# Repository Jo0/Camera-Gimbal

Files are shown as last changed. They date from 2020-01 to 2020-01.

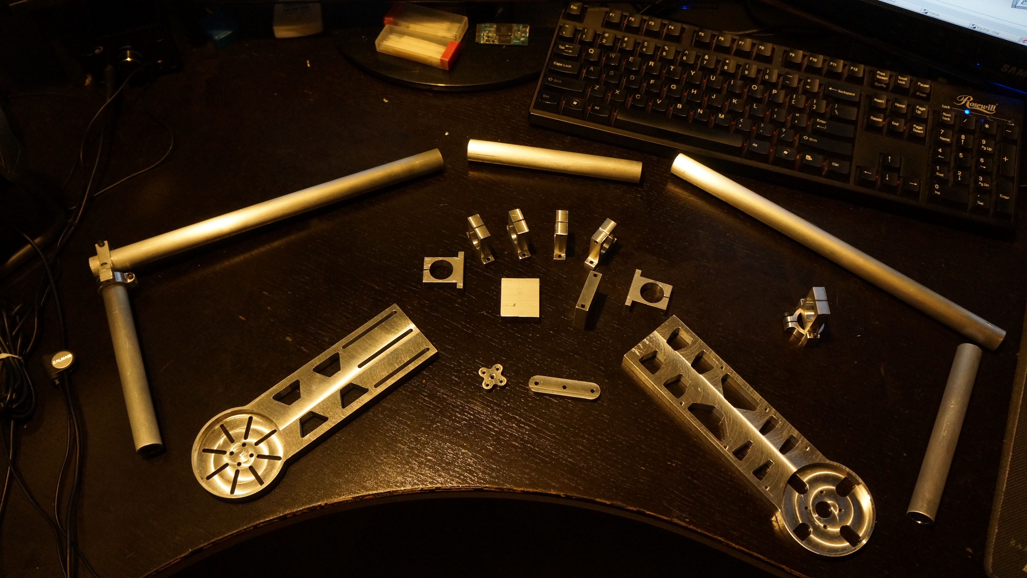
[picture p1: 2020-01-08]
Images/Machined Parts and Assembly/2 - QlwrPvh.jpg

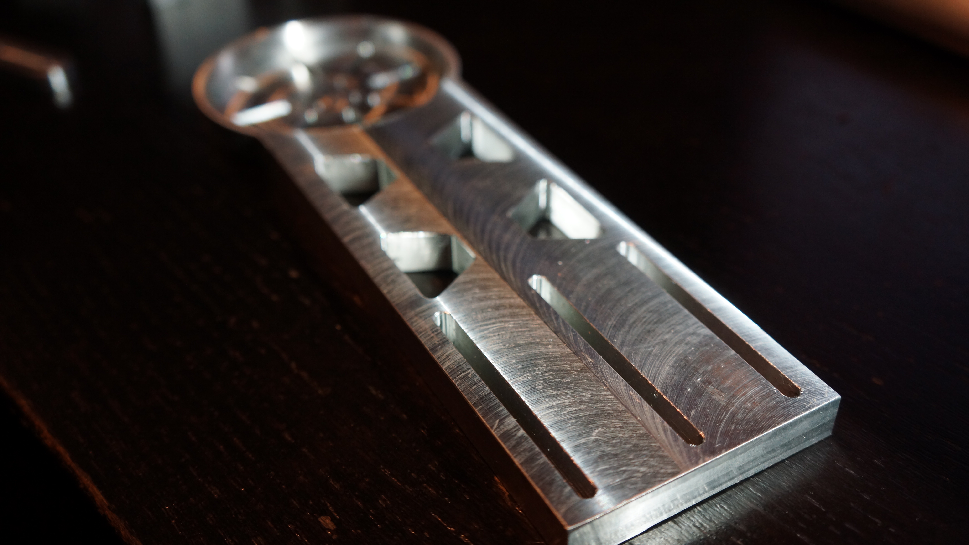
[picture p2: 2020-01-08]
Images/Machined Parts and Assembly/10 - DJeM7ET.jpg

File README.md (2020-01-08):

# Camera Gimbal

## Background

In 2014 I wanted to a camera gimbal. At the time, many great offerings were too expensive (~$500-700) and cheaper products had questionable quality and performance.

I took it upon myself to see if I could design and create my own. My girlfriend's dad (now father in law) is a machinist and was allowed to work on personal projects when off hours. Having no experience with using CAD software I was given access to a machine with SolidWorks and spent a week or so designing the various parts you see here in this repository.

## Materials

- 6061T6 Aluminium Sheet .190" thick
- 6061T6 Aluminium Sheet .750" diameter .125" thick wall
- M3 machine screws
- 685 2RS Premium ABEC3 Bearing 5 x 11 x 5 mm
- 3 x Turnigy HD 5208 Brushless Gimbal Motor
- Turnigy 2200mAh 3S 25C Lipo Pack
- EvvGC 1.3 Gimbal Controller Board with IMU (Inertial Measurement Unit)
  
## Electronics and Software

- EvvGC 1.3 Gimbal Controller Board with IMU (Inertial Measurement Unit)
- [EvvGC Firmware](https://github.com/Jo0/Firmware)
- [EvvGC Electronics](https://github.com/Jo0/Hardware)

## Outcome And Lessons Learned

- Images: 
  - [In this repository](https://github.com/Jo0/Camera-Gimbal/tree/master/Images)
  - [Machined parts and Assembly](https://imgur.com/a/h3jFl?)
  - [Renders](https://imgur.com/a/bzajgdB)
- Videos:
  - [YouTube Playlist Of Test Runs](https://www.youtube.com/playlist?list=PLFWRZ1I7BiI8qetZ2vBfIBI2kLMp9aT8P)
  
### 1. Picking up CAD is faily easy. Creating a good design is difficult

I didn't have a feedback loop of creating a design and prototyping it before finalizing the design. I pretty much relied on intuition (common sense), referencing other designs found online, the simulation of the assembled parts in SolidWorks, and eventually a final review with my father in law before finally machining the parts.

Although my design worked. I feel like I could've gotten a better result if I were able to actually have prototypes of each design iteration before "completing the project".

### 2. CNC Machining is not a magical and easy process

CNC Machining is not a process where you drop a material into a machine, press a button, and your part magically appears.

There's still quite a bit of human intervention in the process.
  - Understanding of materials and their use cases. 
  - Feasibility of the creation of the part(s) based on the design and the machining process(steps) that is necessary to achieve the end result.
  - Programming of the processes(steps) needed to create the part(s)
  - Precision of material and machine setup process

### 3. It's hard to keep costs down and produce a good result

One of the primary goals of the project was to keep costs down. I think I ended up spending ~$225 total to create the gimbal. The cost would've been significantly higher if I had to pay for a machinist to machine my part. Due to machine time and time spent programming the operations to create the parts.

I was able to cut costs on materials by
  - Not having multiple prototypes and only machining when the design was "finalized"
  - Not picking a more established gimbal controller
    - I chose the EvvGC gimbal controller due to the cost of the electronics (~$45) and that it was opensource
    - The other gimbal controller available at the time was the [AlexMos SimpleBGC Controller](https://shop.basecamelectronics.com/) ($150) and the various clone boards available at the time ($50)
      - I didn't want to take a chance on the clone boards due to reports on questionable compatibility on the software to interface with the controller at the time

### 4. There's more to a gimbal than just a frame, brushless motors, and a controller

Although I wanted the gimbal to magically stabilize my camera upon initial setup, I quickly found that there is more configuration to be done to get everything working perfectly.

1. Your gimbal must be balanced, to a reasonable degree, even when it's powered off for it to perform at a reasonable level.
   - While the controller can compensate for everything, it's better to think about the gimbal setup and the controller as an aid to the operator rather than a tool to compensate for the imbalance and instability of the entire system
2. Motor choice must match the load that you plan on putting on the gimbal system.
   - Luckily, I chose motors that were rated higher for the load I was putting on each axis of my gimbal. Had I had decided to choose lower rated motors to cut costs, I think I would've run into issues when mounting heavier cameras like a DSLR.
3. Motor PID tuning is delicate process
   - I may have had difficulty in this area due to the fact that I cut costs and chose an open source gimbal controller. I had a lot of trial and error when tuning the PID settings for the controller to properly control the rates at which the motors compensated for the movement across axes.

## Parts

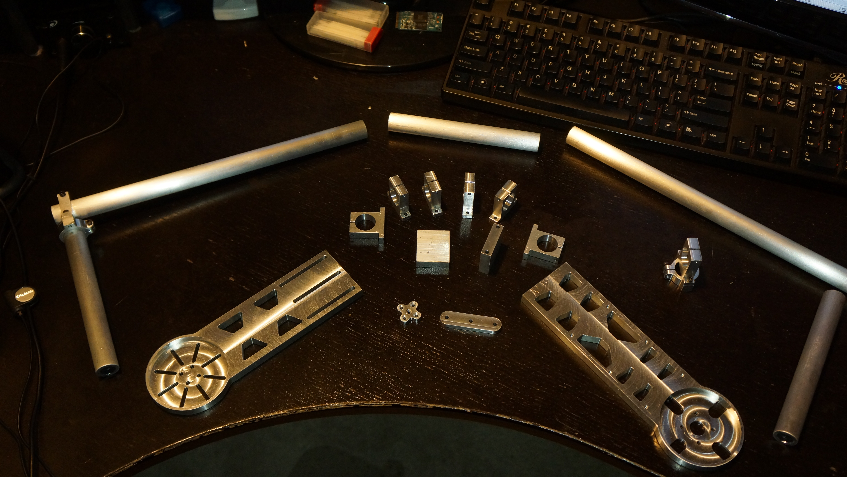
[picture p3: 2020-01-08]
Images/Machined Parts and Assembly/6 - cp2hWf3.jpg

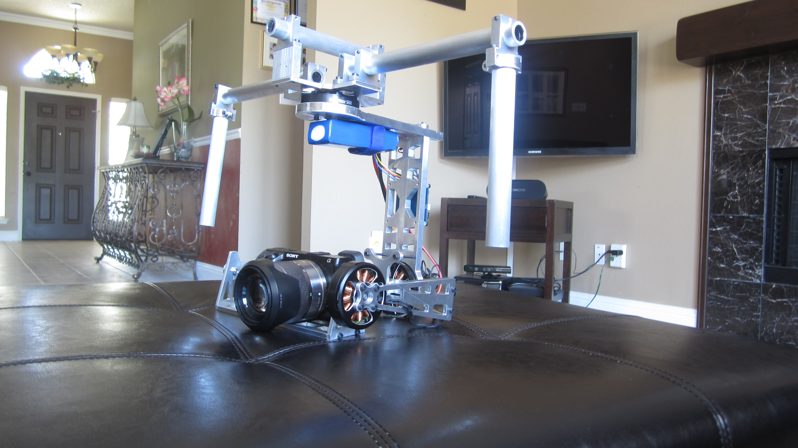
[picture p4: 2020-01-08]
Images/Machined Parts and Assembly/1 - EzWJhA9.jpg

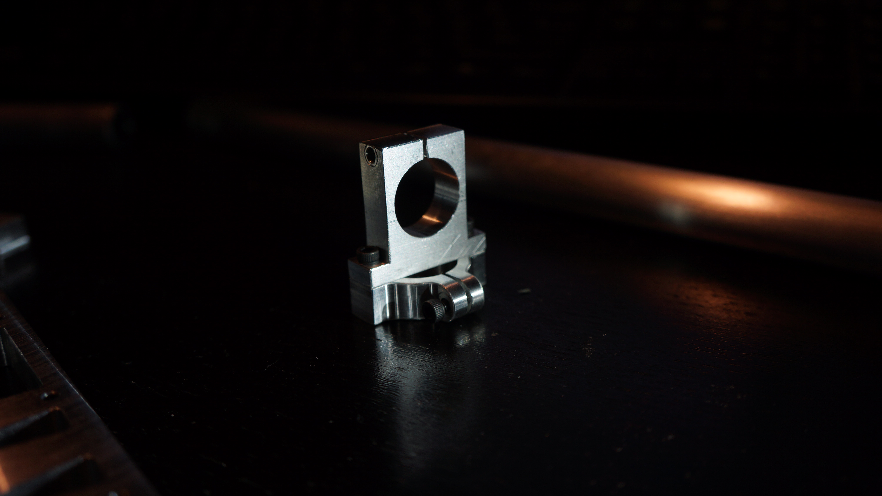
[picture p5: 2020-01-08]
Images/Machined Parts and Assembly/21 - t6TGg4F.jpg

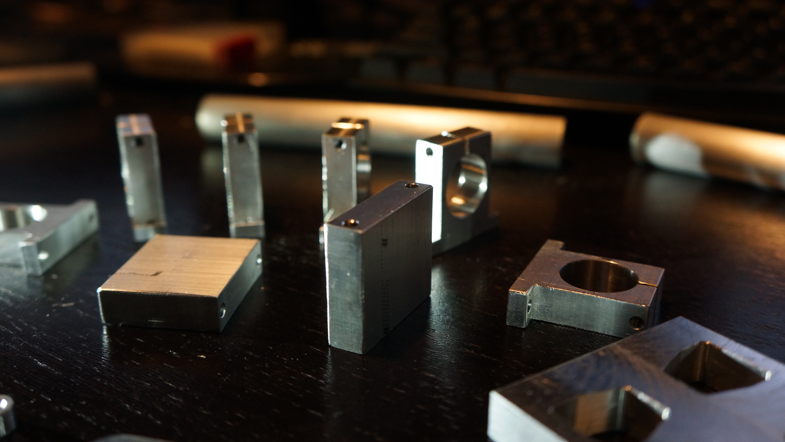
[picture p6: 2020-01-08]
Images/Machined Parts and Assembly/26 - 2xRYPu8.jpg

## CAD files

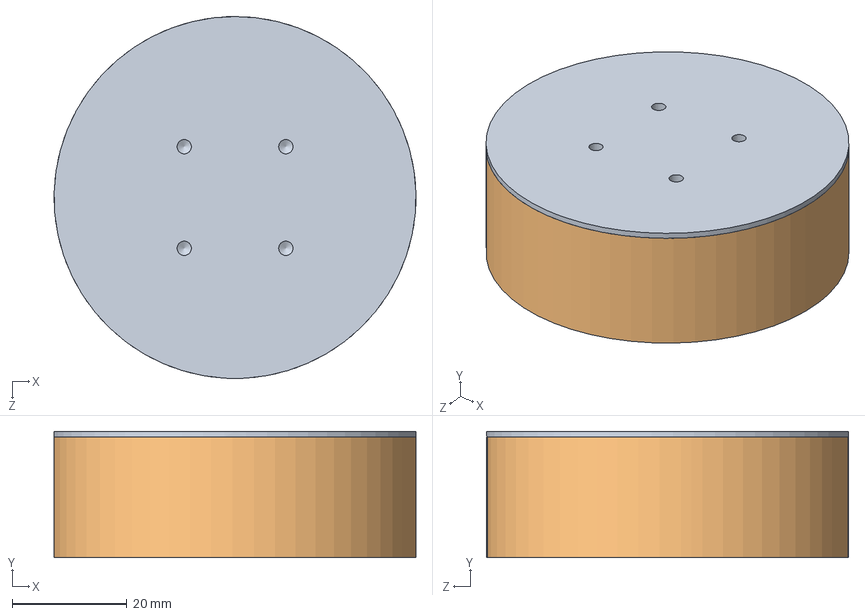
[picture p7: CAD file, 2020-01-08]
Motor Assm.SLDASM
63.0 x 22.0 x 63.0 mm
Mock Motor Bottom
Mock Motor Top

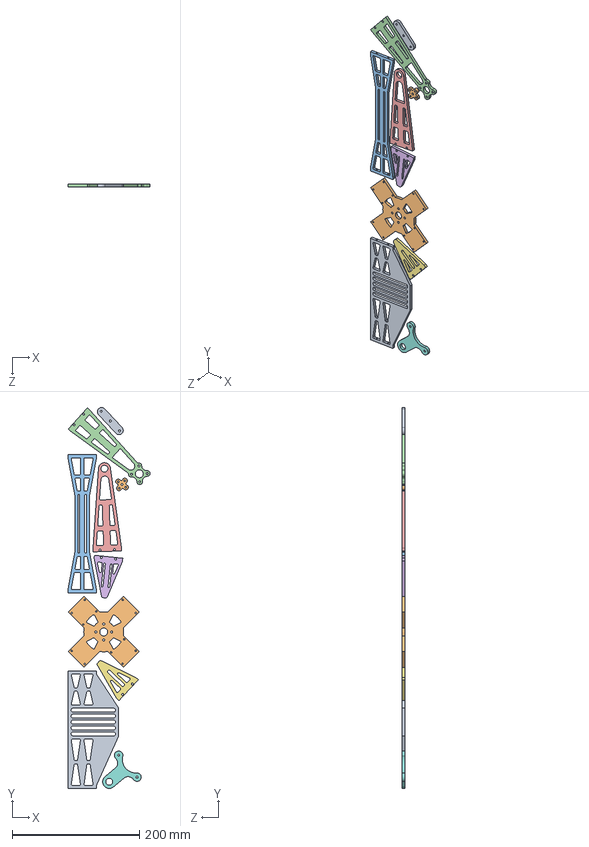
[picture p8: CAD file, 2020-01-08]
NestAssm-Gimbal-5mm.SLDASM
129.4 x 599.6 x 4.76 mm
Camera Tray
Handle Mount
Roll Bar
Pitch Arm Motor
Pitch Arm Bearing
Camera Tray Arm Motor
Camera Tray Arm Bearing
Roll Arm Bearing Support
Yaw Slider Adj Bar
Roll Bar Motor Cross

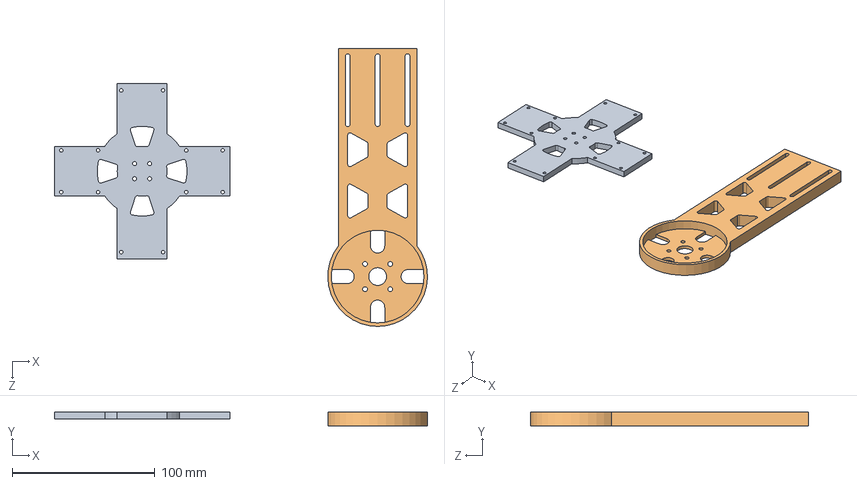
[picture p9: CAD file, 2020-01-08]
Yaw and handle mount.SLDASM
261.7 x 9.53 x 195.0 mm
Handle Mount
Yaw Arm

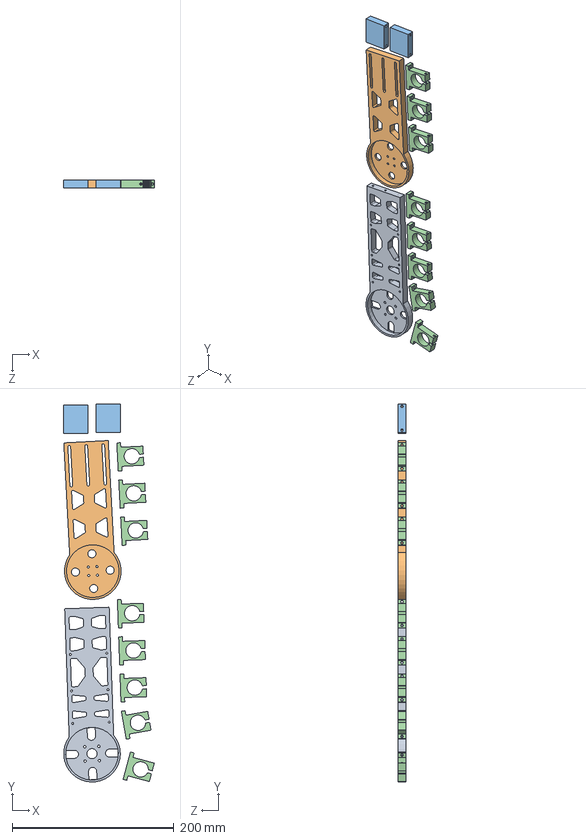
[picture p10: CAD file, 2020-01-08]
NestAssm-Gimbal-10mm.SLDASM
111.9 x 466.7 x 9.53 mm
Roll Arm
Yaw Arm
Spacer x 2
tclamp x 8

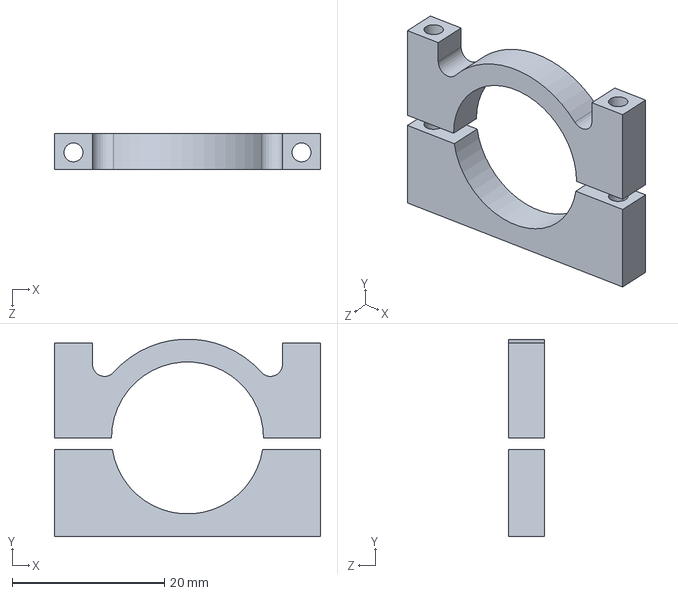
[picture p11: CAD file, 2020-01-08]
CClamp.SLDPRT
35.0 x 26.0 x 4.76 mm

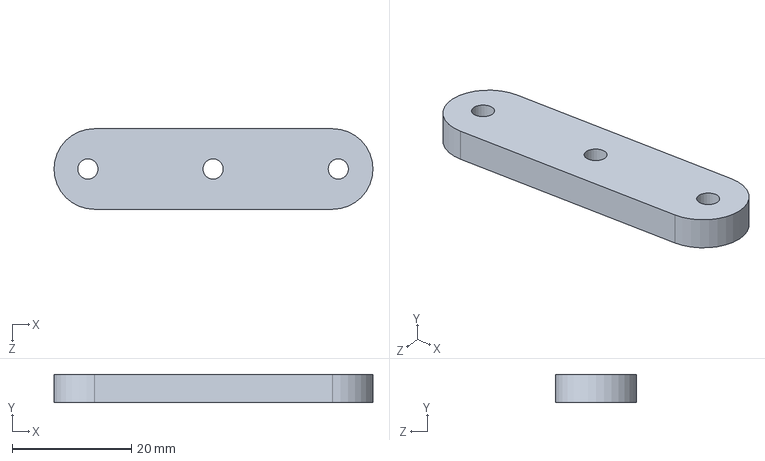
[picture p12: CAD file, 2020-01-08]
Yaw Slider Adj Bar.SLDPRT
53.5 x 4.76 x 13.5 mm

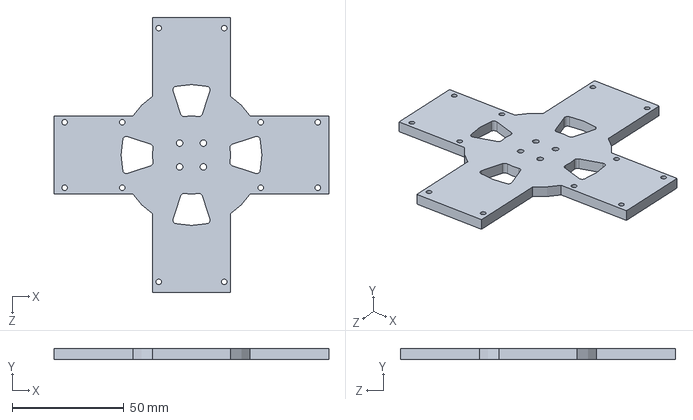
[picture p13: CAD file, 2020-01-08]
Handle Mount.SLDPRT
123.0 x 4.76 x 123.0 mm

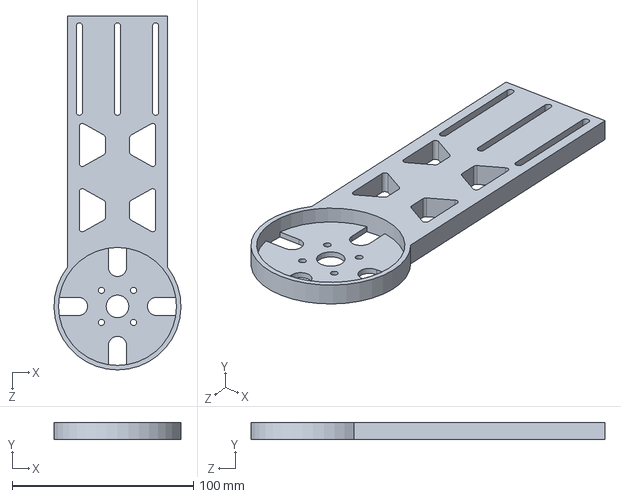
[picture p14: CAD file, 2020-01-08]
Yaw Arm.SLDPRT
70.0 x 9.53 x 195.0 mm

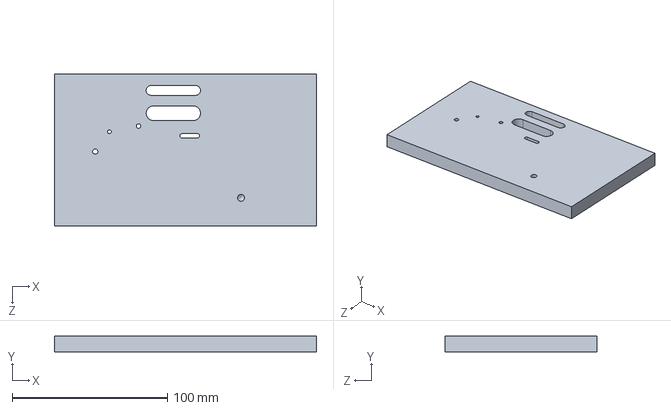
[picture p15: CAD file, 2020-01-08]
Hole Size Test.SLDPRT
168.7 x 10.0 x 97.7 mm

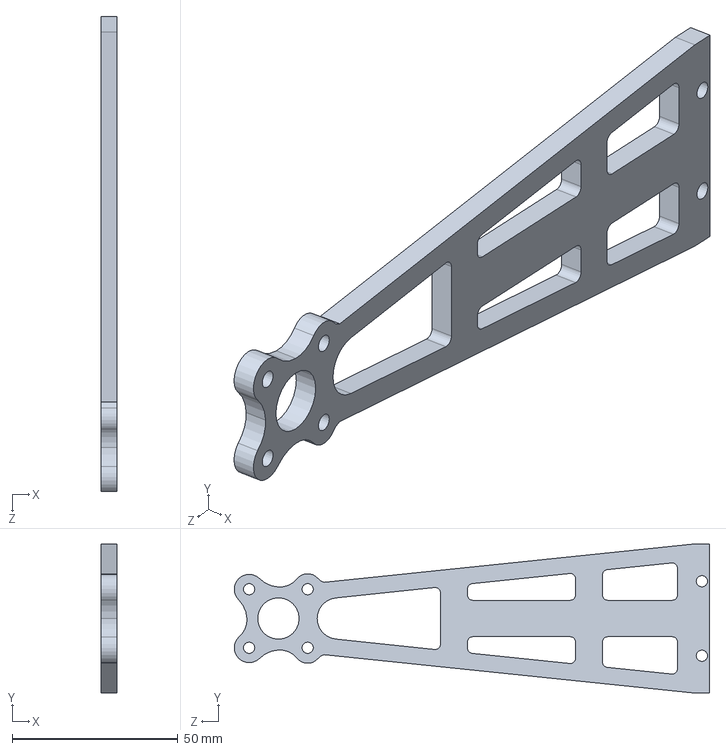
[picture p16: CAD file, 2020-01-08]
Pitch Arm Motor.SLDPRT
4.76 x 45.0 x 143.6 mm

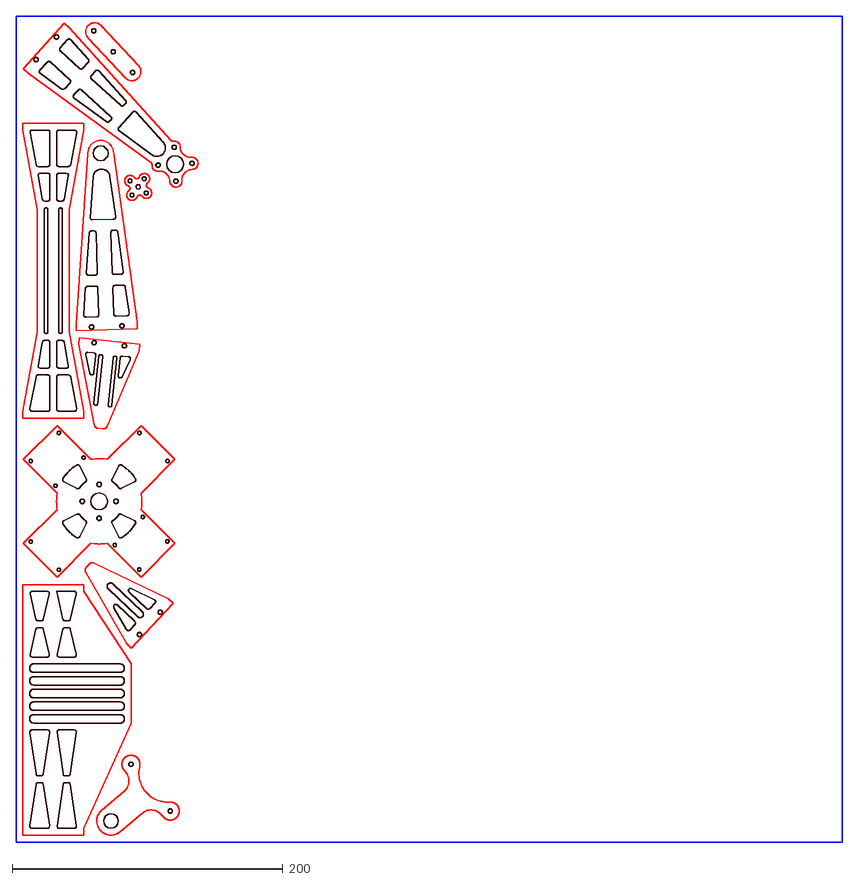
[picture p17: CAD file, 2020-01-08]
NestAssm-Gimbal-5mm_1.dxf
609.6 x 609.6

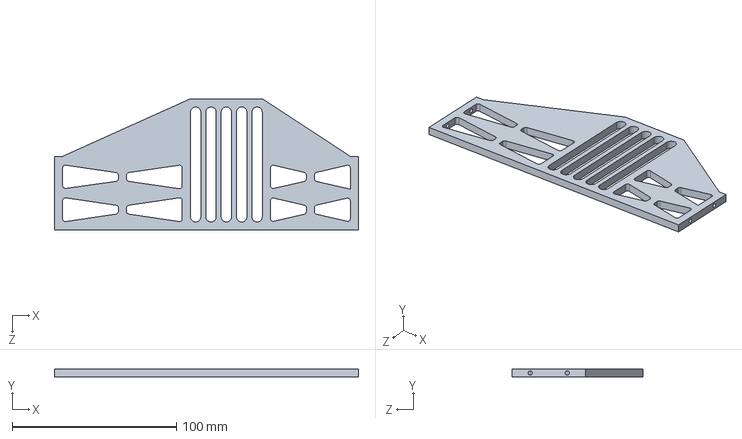
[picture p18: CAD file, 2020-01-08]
Camera Tray.SLDPRT
185.0 x 4.76 x 80.0 mm

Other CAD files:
Assem1.sldasm
NestAssm-Gimbal-10mm-1.sldasm
Yaw and handle mount-1.sldasm
Handle Mount-2.sldprt
Yaw Arm-2.sldprt
Yaw Arm-4.sldprt
12in pipe.SLDPRT
6in pipe.SLDPRT
90deg clamp.SLDPRT
Camera Tray Arm Bearing.SLDDRW
Camera Tray Arm Bearing.SLDPRT
Camera Tray Arm Motor.SLDDRW
Camera Tray Arm Motor.SLDPRT
Camera Tray.SLDDRW
Handle Mount-1.sldprt
Handle Mount-3.sldprt
Handle Mount.SLDDRW
Mock Motor Bottom.SLDPRT
Mock Motor Flat.SLDPRT
Mock Motor Top.SLDPRT
Mock Motor.SLDPRT
NestAssm-Gimbal-10mm.IGS
NestAssm-Gimbal-10mm_1.dxf
NestAssm-Gimbal-5mm.IGS
Pitch Arm Bearing.SLDDRW
Pitch Arm Bearing.SLDPRT
Pitch Arm Motor.SLDDRW
Roll Arm Bearing Support.SLDDRW
Roll Arm Bearing Support.SLDPRT
Roll Arm-1.sldprt
Roll Arm.SLDDRW
Roll Arm.SLDPRT
Roll Bar Motor Cross.SLDDRW
Roll Bar Motor Cross.SLDPRT
Roll Bar.SLDDRW
Roll Bar.SLDPRT
Spacer-1.sldprt
Spacer.SLDDRW
Spacer.SLDPRT
Yaw Arm-1.sldprt
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

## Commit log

2020-01-08 Initial commit of all part files for Camera Gimbal
    [12in pipe.SLDPRT, 6in pipe.SLDPRT, 90deg clamp.SLDPRT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]
2020-01-08 Add rendered images and pictures of machined and assembled parts
2020-01-08 add bearings and screws to material list
